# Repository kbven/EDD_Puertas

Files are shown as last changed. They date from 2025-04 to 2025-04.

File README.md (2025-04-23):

# Disseny de les portes

> **Autors:** Brandon Ventura, Pablo Peñalba.

> **Grup Mati**                             

--------

## Objectivo

Diseño de una una PCB para controlar las puertas.

## Especificaciones

* Mecanismo de motor para el alza cristales con un final de carrera.

* Implementación de mecanismo de seguridad anti-atrapamiento para la ventana con sensor de corriente.

* Sistema con motor por apertura y cierre de la puerta.

* Incluir un módulo de lectura RFID para apertura sin llave.
  
  ## Diagrama de Bloques
  
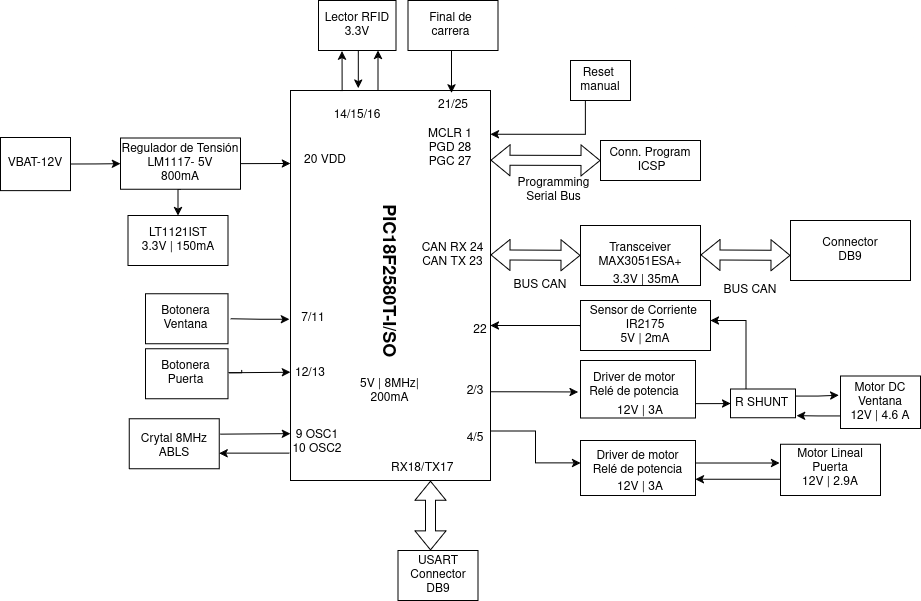
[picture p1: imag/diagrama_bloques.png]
Diagrama_bloques
  
  
  ## Components

| Descripción | Referencia | Package | Datasheet | Proveedor | Precio/unidad | Cantidad |
|:---:|:---:|:---:|:---:|:---:| --- | --- |
| Microcontrolador | PIC18F2580T-I/SO | SOIC-28 | [datasheet](https://ww1.microchip.com/downloads/aemDocuments/documents/OTH/ProductDocuments/DataSheets/39637d.pdf) | [DigiKey](https://www.digikey.es/es/products/detail/microchip-technology/PIC18F2580T-I-SO/739329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) | 7,290 € | 1 |
| Regulador de tensión-5V | LM1117DT-5.0 | TO-252-3  | [datasheet](https://www.ti.com/lit/ds/symlink/lm1117.pdf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) | [Mouser](https://www.mouser.in/ProductDetail/Texas-Instruments/LM1117DT-5.0-NOPB?qs=X1J7HmVL2ZGITaQRKQ6NVA%3D%3D) | 1,610 € | 1 |
| Regulador de tensión 3,3V | LT1121IST-3.3 | SOT-223-3 | [datasheet](https://www.analog.com/media/en/technical-documentation/data-sheets/1121fg.pdf) | [DigiKey](https://www.digikey.at/en/products/detail/analog-devices-inc/LT1121IST-3-3-TRPBF/959066) | 8,190 € | 1 |
| Cristal 8 MHz | AA-8.000MALV-T | SMD | [datasheet](https://www.mouser.es/datasheet/2/417/aa_automotive-14929.pdf) | [Mouser](https://www.mouser.es/ProductDetail/TXC-Corporation/AA-8.000MALV-T?qs=02P6ycQEDWEs8mIQTVoxpQ%3D%3D) | 0,779 € | 1 |
| Pulsadores | 3-1437565-0 | SMD | [datasheet](https://www.mouser.es/datasheet/2/418/7/ENG_CD_2_1437565_7_V-2027970.pdf) | [Mouser](https://www.mouser.es/ProductDetail/TE-Connectivity-PB/3-1437565-0?qs=%2FwXgF%2FfIho%2FDAgSy8ONeew%3D%3D) | 0,266 € | 5 |
| Transceiver | MAX3051ESA+ | SOIC-8 | [datasheet](https://www.mouser.es/datasheet/2/609/MAX3051-3469944.pdf) | [Mouser](https://www.mouser.es/ProductDetail/Analog-Devices-Maxim-Integrated/MAX3051ESA+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) | 3,820 € | 1 |
| Módulo RFID | DLP-RFID2 | THT | [datasheet](https://www.mouser.es/datasheet/2/117/dlp-rfid2-ds-v114-1374531.pdf) | [Mouser](https://www.mouser.es/ProductDetail/DLP-Design/DLP-RFID2?qs=7edrXduW%2FNsZxdz8dNHO%2BQ%3D%3D) | 36,050 € | 1 |
| Conector coaxial | Conector coaxial RS | THT | [datasheet](https://docs.rs-online.com/062e/A700000007510792.pdf) | [RS](https://es.rs-online.com/web/p/conectores-coaxiales/5464049) | 9,630 € | 1 |
| Sensor de Corriente | IR2175STRPBF | SOIC-8 | [datasheet](https://www.mouser.es/datasheet/2/196/Infineon_IR2175_S__DataSheet_v01_00_EN-3362704.pdf) | [Mouser](https://www.mouser.es/ProductDetail/Infineon-Technologies/IR2175STRPBF?qs=2r01AXMCG3Mz96toc2YS0Q%3D%3D) | 3,080 € | 1 |
| Relé de potencia | G6E | THT | [datasheet](https://docs.rs-online.com/8949/A700000008621017.pdf) | [RS](https://es.rs-online.com/web/p/reles-de-potencia/0376593) | 6,180 € | 4 |
| Conector DB9 | 2311765-2 | THT | [datasheet](https://www.mouser.es/datasheet/2/418/7/ENG_CD_2311765_D-2072969.pdf) | [Mouser](https://www.mouser.es/ProductDetail/TE-Connectivity/2311765-2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) | 2,760 € | 2 |
| MOSFET P-Channel | AO3401A | SOT-23-3  | [datasheet](https://www.aosmd.com/sites/default/files/res/datasheets/AO3401A.pdf) | [Digikey](https://www.digikey.es/es/products/detail/alpha-omega-semiconductor-inc/AO3401A/1855773) | 0,420 € | 4 |
| Led verde | LTST-C150KGKT | 1206 | [datasheet](https://www.mouser.es/datasheet/2/239/LTST_C150KGKT-1143771.pdf) | [Mouser](https://www.mouser.es/ProductDetail/LITEON/LTST-C150KGKT?qs=G7lFeYdtIHB%2FzaFKBwEyXw%3D%3D) | 0,171 € | 1 |
| Pin Header 1x3 | 61300311121 | THT | [datasheet](https://www.we-online.com/components/products/datasheet/61300311121.pdf) | [DigiKey](https://www.digikey.es/es/products/detail/w%C3%BCrth-elektronik/61300311121/4846825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) | 0,110 € | 1 |
| Pin Header 1x5 | 61300511121 | THT | [datasheet](https://www.we-online.com/components/products/datasheet/61300511121.pdf) | [DigiKey](https://www.digikey.es/es/products/detail/w-rth-elektronik/61300511121/4846831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) | 0,220 € | 3 |
| Connector screw 1x2 | 1729128 | --- | [datasheet](https://www.phoenixcontact.com/en-us/products/printed-circuit-board-terminal-mkdsn-15-2-508-1729128?type=pdf) | [Mouser](https://www.mouser.es/ProductDetail/Phoenix-Contact/1729128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) | 1,020 € | 3 |
| Connector screw 1x3 | 1751251 | --- | [datasheet](https://www.phoenixcontact.com/en-us/products/printed-circuit-board-terminal-mkds-1-3-35-1751251?type=pdf) | [Mouser](https://www.mouser.es/ProductDetail/Phoenix-Contact/1751251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) | 1,680 € | 2 |
| Resistencias 10K | RK73G2BTTD1002F | 1206 | [datasheet](https://www.koaspeer.com/pdfs/RK73G.pdf) | [Mouser](https://www.mouser.es/ProductDetail/KOA-Speer/RK73G2BTTD1002F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) | 0,241 € | 15 |
| Resistencia 60 | RP73PF1J60R4BTDF | 0603 | [datasheet](https://www.mouser.es/datasheet/2/418/10/ENG_DS_1773272_M1-1588495.pdf) | [Mouser](https://www.mouser.es/ProductDetail/TE-Connectivity-Holsworthy/RP73PF1J60R4BTDF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) | 0,456 € | 1 |
| Resistencia 1K | RNCA0603BTE1K00 | 0603 | [datasheet](https://www.mouser.es/datasheet/2/385/SEI_RNCA-3473065.pdf) | [Mouser](https://www.mouser.es/ProductDetail/SEI-Stackpole/RNCA0603BTE1K00?qs=i8QVZAFTkqR0RAUMHohaTQ%3D%3D) | 0,228 € | 1 |
| Resistencia shunt | WSHM2818R1000FEA | SMD | [datasheet](https://www.vishay.com/docs/30188/wshm2818.pdf) | [Mouser](https://www.mouser.es/ProductDetail/Vishay-Dale/WSHM2818R1000FEA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) | 1,370 € | 1 |
| 10u | ECA-1CHG101I | THT | [datasheet](https://industrial.panasonic.com/cdbs/www-data/pdf/RDF0000/ABA0000C1218.pdf) | [Mouser](https://www.mouser.es/ProductDetail/Panasonic/ECA-1CM100I?qs=fcM5arftASvKR70PPIzFqA%3D%3D) | 0,152 € | 3 |
| 1u | C0805C105K4RACAUTO  | 0805 | [datasheet](https://www.mouser.es/datasheet/2/447/KEM_C1023_X7R_AUTO_SMD-3316698.pdf) | [Mouser](https://www.mouser.es/ProductDetail/KEMET/C0805C105K4RACAUTO?qs=OHu5RF0w3QprP0D5VzlqaQ%3D%3D) | 0,152 € | 1 |
| 100n | C1206C104K4RACTU | 1206 | [datasheet](https://www.mouser.es/datasheet/2/447/KEM_C1002_X7R_SMD-3316098.pdf) | [Mouser](https://www.mouser.es/ProductDetail/KEMET/C1206C104K4RACTU?qs=NAOyRStS94fKvqJx0gg6JQ%3D%3D) | 0,095 € | 7 |
| 21p | 0504N220J500P | 0504 | [datasheet](https://www.knowlescapacitors.com/getattachment/ddd08fe0-16c1-4f86-944e-edc3fc04fb57/X7R.aspx) | [DigiKey](https://www.digikey.es/es/products/detail/knowles-novacap/0504N220J500P/21849946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) | 0,620 € | 2 |
| D6,D7,D8,D9 | SR1202 A0G | THT | [datasheet](https://services.taiwansemi.com/storage/resources/datasheet/SR1202%20SERIES_G2105.pdf) | [Mouser](https://www.mouser.es/ProductDetail/Taiwan-Semiconductor/SR1202-A0G?qs=mAH9sUMRCtsYw%2FEG19A30A%3D%3D) | 0,384 € | 4 |
| D4,D5 | SBR12A45SD1-T | THT | [datasheet](https://www.diodes.com/assets/Datasheets/SBR12A45SD1.pdf) | [Mouser](https://www.mouser.es/ProductDetail/Diodes-Incorporated/SBR12A45SD1-T?qs=oUsD4qhOtFxVeI%252BTfVYIRA%3D%3D) | 0,485 € | 2 |
| D2 | SR1203H | THT | [datasheet](https://services.taiwansemi.com/storage/resources/datasheet/SR1202%20SERIES_G2105.pdf) | [Mouser](https://www.mouser.es/ProductDetail/Taiwan-Semiconductor/SR1203H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) | 0,384 € | 1 |
| D3 | SBR10U45SD1-T | THT | [datasheet](https://www.diodes.com/assets/Datasheets/SBR10U45SD1.pdf) | [Mouser](https://www.mouser.es/ProductDetail/Diodes-Incorporated/SBR10U45SD1-T?qs=oUsD4qhOtFyWKufSWj8qkg%3D%3D) | 0,912 € | 1 |

##Motores y final de carrera

| Descripción | Referencia | Datasheet | Proveedor | Cantidad |
|:---:|:---:|:---:|:---:| --- |
| Motor Lineal | Actuador lineal 12VDC 800N 2,9A | | [Transmotec](https://www.transmotec.es/product/dla-12-30-a-50-ip65/?vat=true) | 1 |
| Motor DC | Motor DC RS PRO | [datasheet](https://docs.rs-online.com/6e47/A700000007082069.pdf) | [Rs](https://es.rs-online.com/web/p/motores-dc/3213186) | 1 |
| Final de carrera | Palanca de Rodillo RS PRO | [datasheet](https://docs.rs-online.com/2b32/A700000008919438.pdf) | [Rs](https://es.rs-online.com/web/p/interruptores-final-de-carrera/9026871) | 2 |

## Historial de cambios

| Data | Autor | Branch | Descripción |
| --- | --- | --- | --- |
| 26/03/2025 | B.Ventura | Main | Readme y Esquemático |
| 26/03/2025 | B.Ventura | Main | Diagrama de Bloques |
| 28/03/2025 | B.Ventura | Main | Terminales y Diodos |
| 28/03/2025 | P.Peñalba | Main | Etiquetas,Botonera y Buck converter |
| 01/04/2025 | B.Ventura | Main | Corrección del esquema, terminal screw terminals y layout v1 |
| 09/04/2025 | B.Ventura | Main | cambio de posición pines, cambio de terminales final de carrera y corrección error grid |
| 09/04/2025 | B.Ventura/P.Peñalba | Main | layout versión 2, reglas de diseño JLCPCB |
| 12/04/2025 | B.Ventura/P.Peñalba | Main | Corrección de las pistas layout y planos |
| 21/04/2025 | B.Ventura | Main | Presupuesto |

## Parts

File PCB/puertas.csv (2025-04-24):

# | Reference | Footprint | Qty | Value
1 | C1,C2,C7,C8,C9,C10,C13 | Capacitor_SMD:C_1206_3216Metric | 7 | 100n
2 | C3,C4 | Capacitor_THT:CP_Radial_D5.0mm_P2.50mm | 2 | 10u
3 | C5,C6 | Capacitor_SMD:C_0504_1310Metric | 2 | 21p
4 | C11 | Capacitor_THT:CP_Radial_D6.3mm_P2.50mm | 1 | 10u
5 | C12 | Capacitor_SMD:C_0805_2012Metric | 1 | 1uF
6 | D1 | LED_SMD:LED_1206_3216Metric | 1 | LED
7 | D2,D4,D5,D6,D7,D8,D9 | Diode_THT:D_DO-201AD_P12.70mm_Horizontal | 7 | D
8 | D3 | Diode_THT:D_DO-15_P12.70mm_Horizontal | 1 | D_Zener
9 | IC1 | MAX3051ESA+:SOIC127P600X175-8N | 1 | MAX3051ESA+
10 | IC2 | IR2175STRPBF:SOIC127P600X175-8N | 1 | IR2175STRPBF
11 | J1 | Connector_Dsub:DSUB-9_Pins_Horizontal_P2.77x2.84mm_EdgePinOffset4.94mm_Housed_MountingHolesOffset4.94mm | 1 | DE9_USART
12 | J2 | Connector_PinHeader_2.54mm:PinHeader_1x05_P2.54mm_Vertical | 1 | ICSP
13 | J3 | Connector_Dsub:DSUB-9_Pins_Horizontal_P2.77x2.84mm_EdgePinOffset4.94mm_Housed_MountingHolesOffset4.94mm | 1 | DE9_CAN
14 | J4 | Connector_Coaxial:BNC_TEConnectivity_1478035_Horizontal | 1 | Conn_Coaxial
15 | J5 | TerminalBlock_Phoenix:TerminalBlock_Phoenix_MKDS-3-2-5.08_1x02_P5.08mm_Horizontal | 1 | BAT_CONN
16 | J6 | Connector_PinHeader_2.54mm:PinHeader_1x03_P2.54mm_Vertical | 1 | PROG
17 | J7 | Connector_PinHeader_2.54mm:PinHeader_1x05_P2.54mm_Vertical | 1 | DOOR
18 | J8 | Connector_PinHeader_2.54mm:PinHeader_1x05_P2.54mm_Vertical | 1 | WINDOW
19 | J9 | TerminalBlock_Phoenix:TerminalBlock_Phoenix_MKDS-3-2-5.08_1x02_P5.08mm_Horizontal | 1 | motor_lineal
20 | J10 | TerminalBlock_Phoenix:TerminalBlock_Phoenix_MKDS-3-3-5.08_1x03_P5.08mm_Horizontal | 1 | FINAL_ALTO
21 | J12 | TerminalBlock_Phoenix:TerminalBlock_Phoenix_MKDS-3-2-5.08_1x02_P5.08mm_Horizontal | 1 | motor_dc
22 | J13 | TerminalBlock_Phoenix:TerminalBlock_Phoenix_MKDS-3-3-5.08_1x03_P5.08mm_Horizontal | 1 | FINAL_BAJO
23 | K1,K2,K3,K4 | Relay_THT:Relay_SPDT_Omron_G6E | 4 | G6E
24 | pull-down1,pull-down2,pull-down3,pull-down4,R11,R12,R13,R16,R17 | Capacitor_SMD:C_1206_3216Metric | 9 | 10k
25 | Q1,Q2,Q3,Q4 | Package_TO_SOT_SMD:SOT-23 | 4 | AO3401A
26 | R1 | Resistor_SMD:R_1206_3216Metric_Pad1.30x1.75mm_HandSolder | 1 | 10K
27 | R2 | Resistor_SMD:R_0603_1608Metric | 1 | 60
28 | R3,R4,R5,R6,R8 | Resistor_SMD:R_1206_3216Metric | 5 | 10k
29 | R7 | Resistor_SMD:R_0603_1608Metric | 1 | 1k
30 | R9 | Resistor_SMD:R_Shunt_Ohmite_LVK25 | 1 | R_Shunt
31 | R10 | Capacitor_SMD:C_1206_3216Metric | 1 | 0
32 | S1,S2,S3,S6,S7 | 3-1437565-0:314375650 | 5 | 3-1437565-0
33 | U1 | DLP-RFID2:DLP-RFID2 | 1 | DLP-RFID2
34 | U3 | LT1121IST-3.3-TRPBF:SOT-223_ST_LIT | 1 | LT1121IST-3.3-TRPBF
35 | U4 | PIC18F2580T_I_SO:SOIC28-W_MC_MCH | 1 | PIC18F2580T-I/SO
36 | U5 | Package_TO_SOT_SMD:TO-252-3_TabPin2 | 1 | LM1117DT-5.0
37 | Y2 | AA-8.000MALV-T:AA8000MALVT | 1 | AA-8.000MALV-T

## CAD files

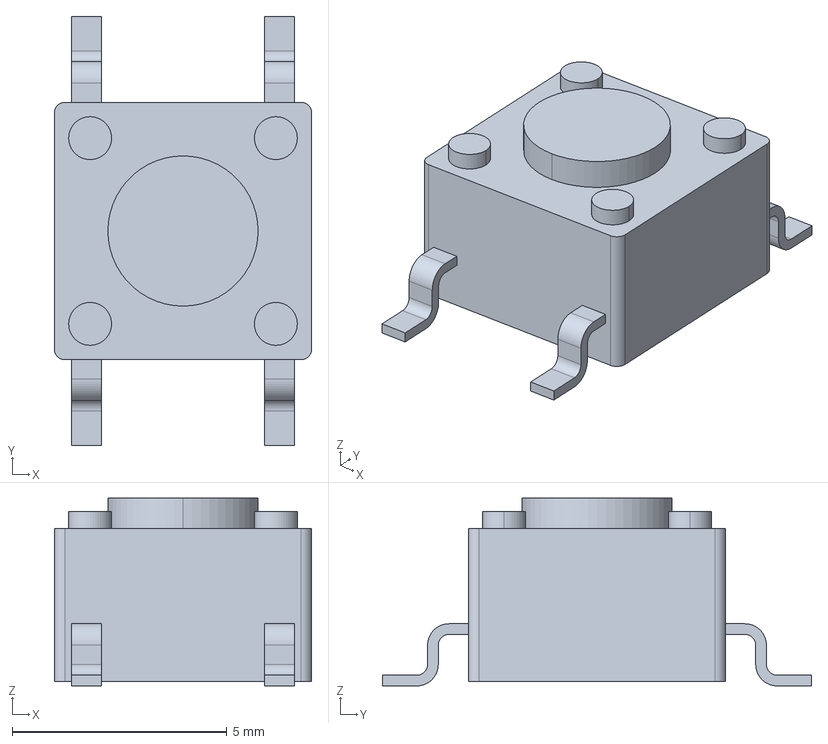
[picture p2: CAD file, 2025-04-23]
PCB/componentes/3-1437565-0/3D/3-1437565-0.stp
6.00 x 10.0 x 4.38 mm

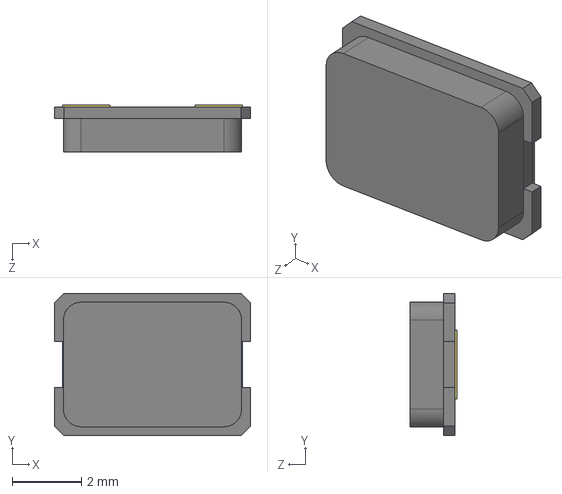
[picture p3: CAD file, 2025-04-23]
PCB/componentes/AA-8.000MALV-T/3D/AA-8.000MALV-T.stp
5.67 x 4.12 x 1.35 mm

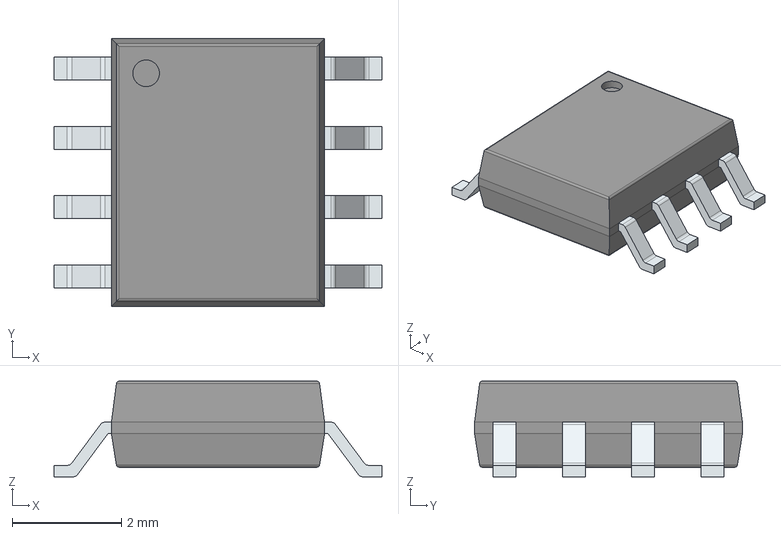
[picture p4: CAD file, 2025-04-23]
PCB/componentes/IR2175STRPBF/3D/IR2175STRPBF.stp
6.00 x 4.90 x 1.75 mm
PinsArrayLR

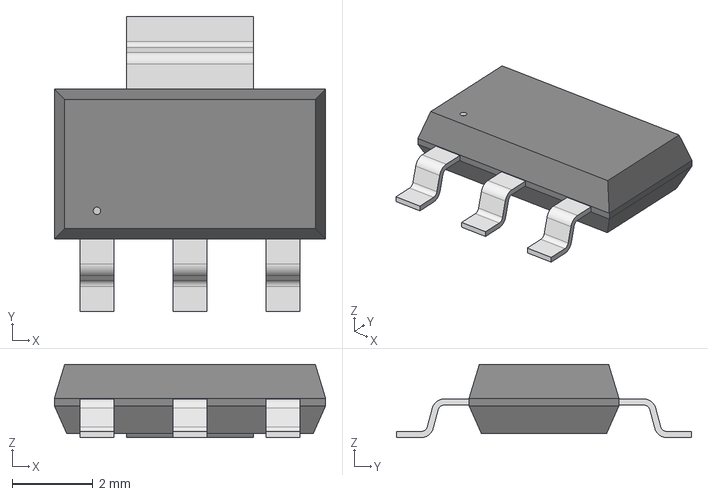
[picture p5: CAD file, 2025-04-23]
PCB/componentes/LT1121IST/3d/SOT-223_ST_LIT.step
6.71 x 7.29 x 1.81 mm

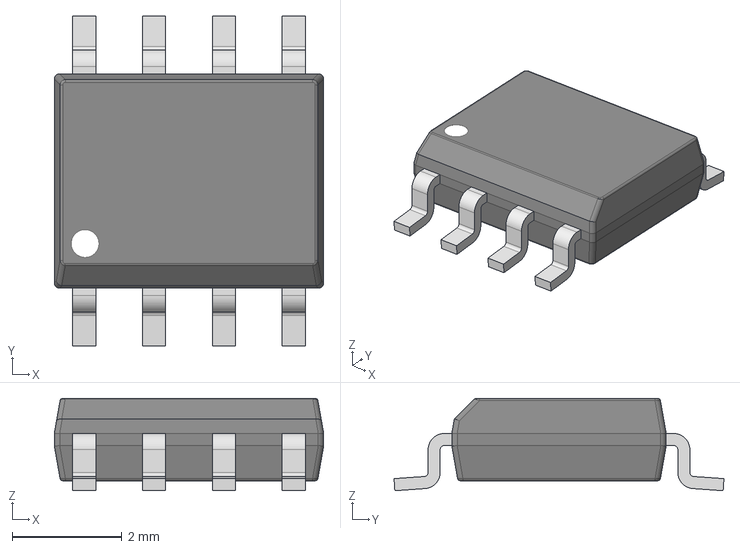
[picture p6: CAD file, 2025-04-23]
PCB/componentes/MAX3051ESA+/3D/MAX3051ESA+T.stp
4.90 x 6.00 x 1.68 mm

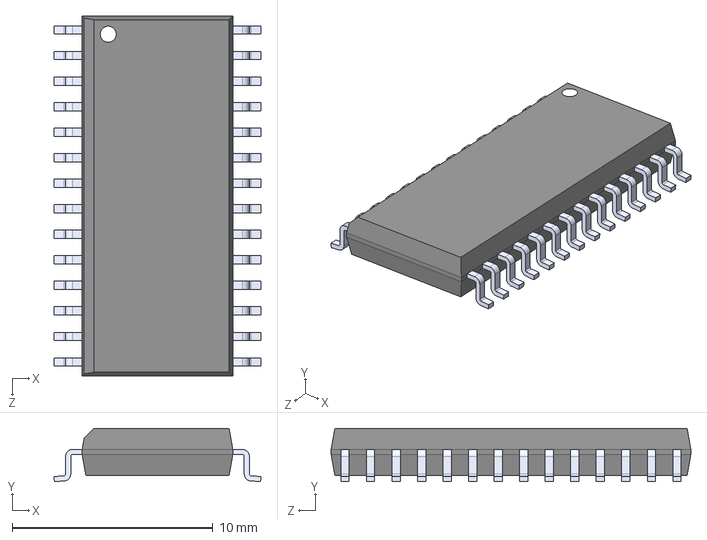
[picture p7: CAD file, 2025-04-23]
PCB/componentes/PIC18F2580T_I_SO/3d model/PIC18F2580T-I_SO.STEP
10.3 x 2.65 x 17.9 mm

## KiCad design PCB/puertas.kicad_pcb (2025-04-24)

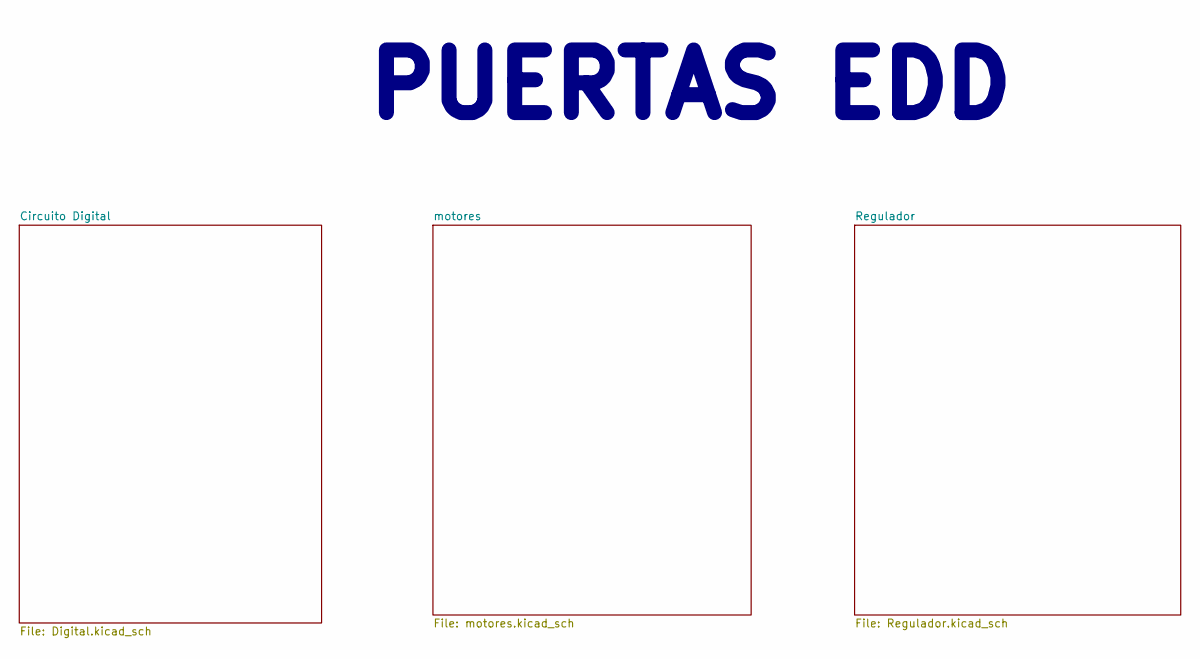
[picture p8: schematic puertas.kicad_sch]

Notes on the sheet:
PUERTAS EDD

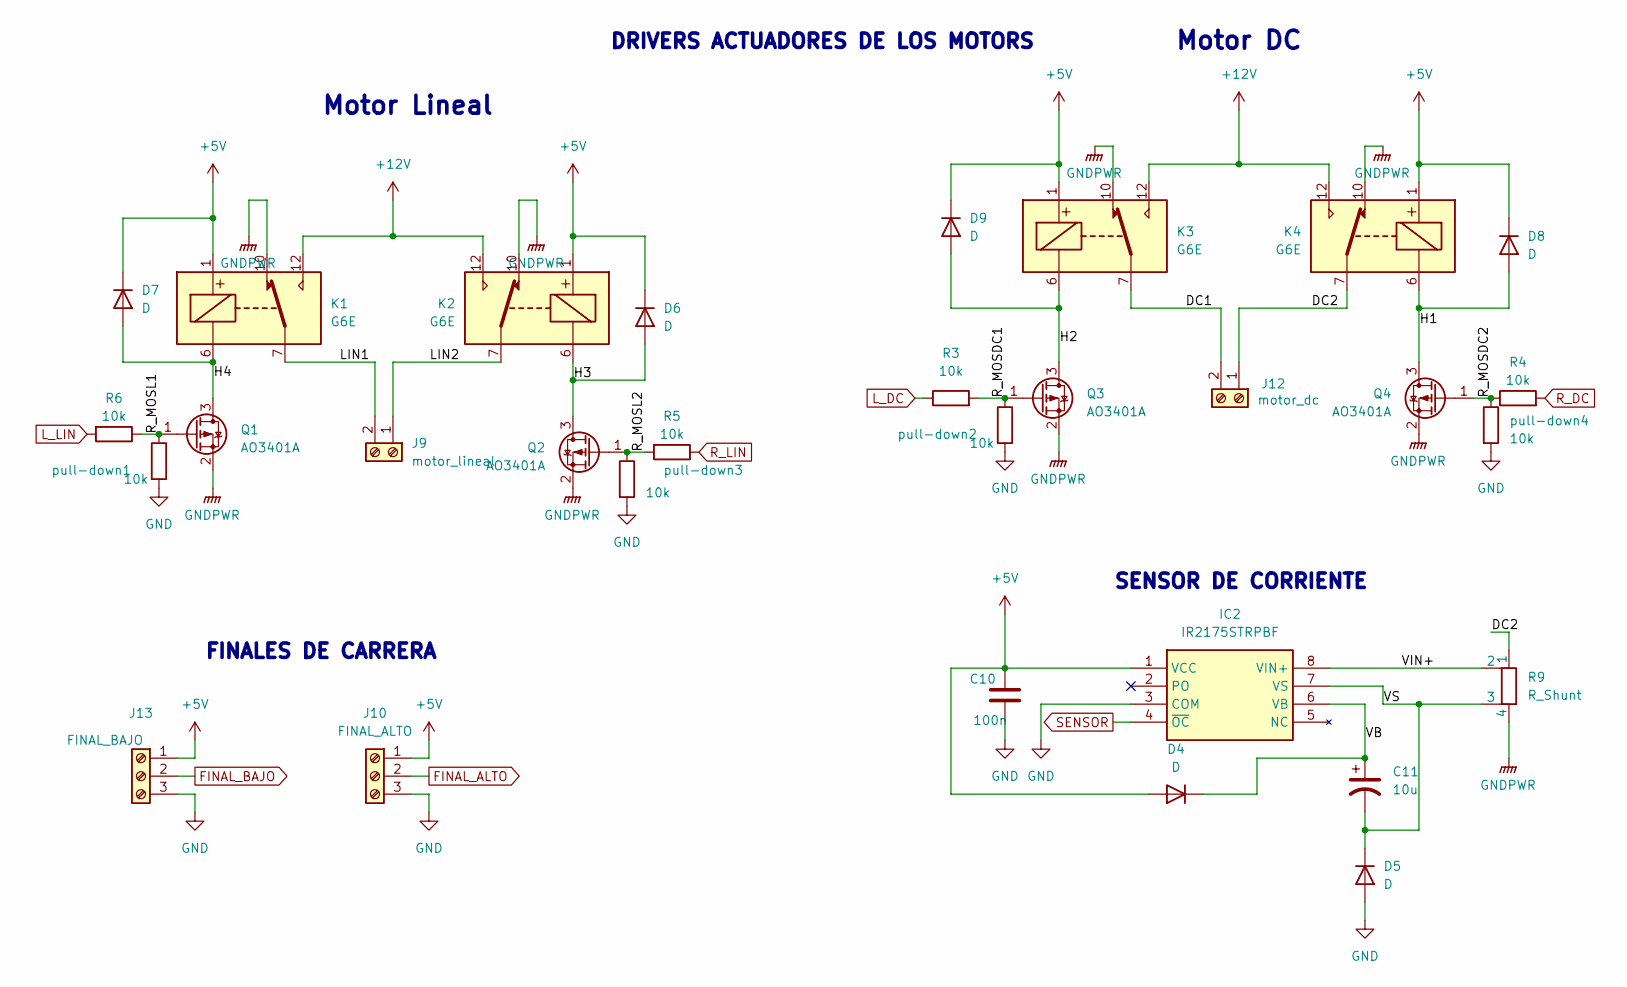
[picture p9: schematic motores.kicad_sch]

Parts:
C10: 100n; C_1206_3216Metric
C11: 10u; CP_Radial_D6.3mm_P2.50mm
D4, D5, D6, D7, D8, D9: D; D_DO-201AD_P12.70mm_Horizontal
IC2: IR2175STRPBF; SOIC127P600X175-8N; Mouser Part Number 942-IR2175STRPBF
J9: motor_lineal; TerminalBlock_Phoenix_MKDS-3-2-5.08_1x02_P5.08mm_Horizontal
J10: FINAL_ALTO; TerminalBlock_Phoenix_MKDS-3-3-5.08_1x03_P5.08mm_Horizontal
J12: motor_dc; TerminalBlock_Phoenix_MKDS-3-2-5.08_1x02_P5.08mm_Horizontal
J13: FINAL_BAJO; TerminalBlock_Phoenix_MKDS-3-3-5.08_1x03_P5.08mm_Horizontal
K1, K2, K3, K4: G6E; Relay_SPDT_Omron_G6E
Q1, Q2, Q3, Q4: AO3401A; SOT-23
R3, R4, R5, R6: 10k; R_1206_3216Metric
R9: R_Shunt; R_Shunt_Ohmite_LVK25
pull-down1, pull-down2, pull-down3, pull-down4: 10k; C_1206_3216Metric

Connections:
+5V: C10.1, D4.2 (A), D6.1 (K), D7.1 (K), D8.1 (K), D9.1 (K), IC2.1 (VCC), J10.1, J13.1, K1.1, K2.1, K3.1, K4.1; also elsewhere on the board
+12V: K1.12, K2.12, K3.12, K4.12; also elsewhere on the board
/motores/DC1: J12.2, K3.7
/motores/DC2: J12.1, K4.7, R9.1
/motores/H1: D8.2 (A), K4.6, Q4.3 (D)
/motores/H2: D9.2 (A), K3.6, Q3.3 (D)
/motores/H3: D6.2 (A), K2.6, Q2.3 (D)
/motores/H4: D7.2 (A), K1.6, Q1.3 (D)
/motores/LIN1: J9.2, K1.7
/motores/LIN2: J9.1, K2.7
/motores/R_MOSDC1: Q3.1 (G), R3.2, pull-down2.1
/motores/R_MOSDC2: Q4.1 (G), R4.1, pull-down4.1
/motores/R_MOSL1: Q1.1 (G), R6.1, pull-down1.1
/motores/R_MOSL2: Q2.1 (G), R5.2, pull-down3.1
/motores/VB: C11.1, D4.1 (K), IC2.6 (VB)
/motores/VIN+: IC2.8 (VIN+), R9.2
/motores/VS: C11.2, D5.1 (K), IC2.7 (VS), R9.3
FINAL_ALTO: J10.2; also elsewhere on the board
FINAL_BAJO: J13.2; also elsewhere on the board
GND: C10.2, D5.2 (A), IC2.3 (COM), J10.3, J13.3, pull-down1.2, pull-down2.2, pull-down3.2, pull-down4.2; also elsewhere on the board
GNDPWR: K1.10, K2.10, K3.10, K4.10, Q1.2 (S), Q2.2 (S), Q3.2 (S), Q4.2 (S), R9.4; also elsewhere on the board
L_DC: R3.1; also elsewhere on the board
L_LIN: R6.2; also elsewhere on the board
R_DC: R4.2; also elsewhere on the board
R_LIN: R5.1; also elsewhere on the board
SENSOR: IC2.4 (~OC); also elsewhere on the board

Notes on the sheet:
FINALES DE CARRERA
Motor DC
Motor Lineal
DRIVERS ACTUADORES DE LOS MOTORS
SENSOR DE CORRIENTE

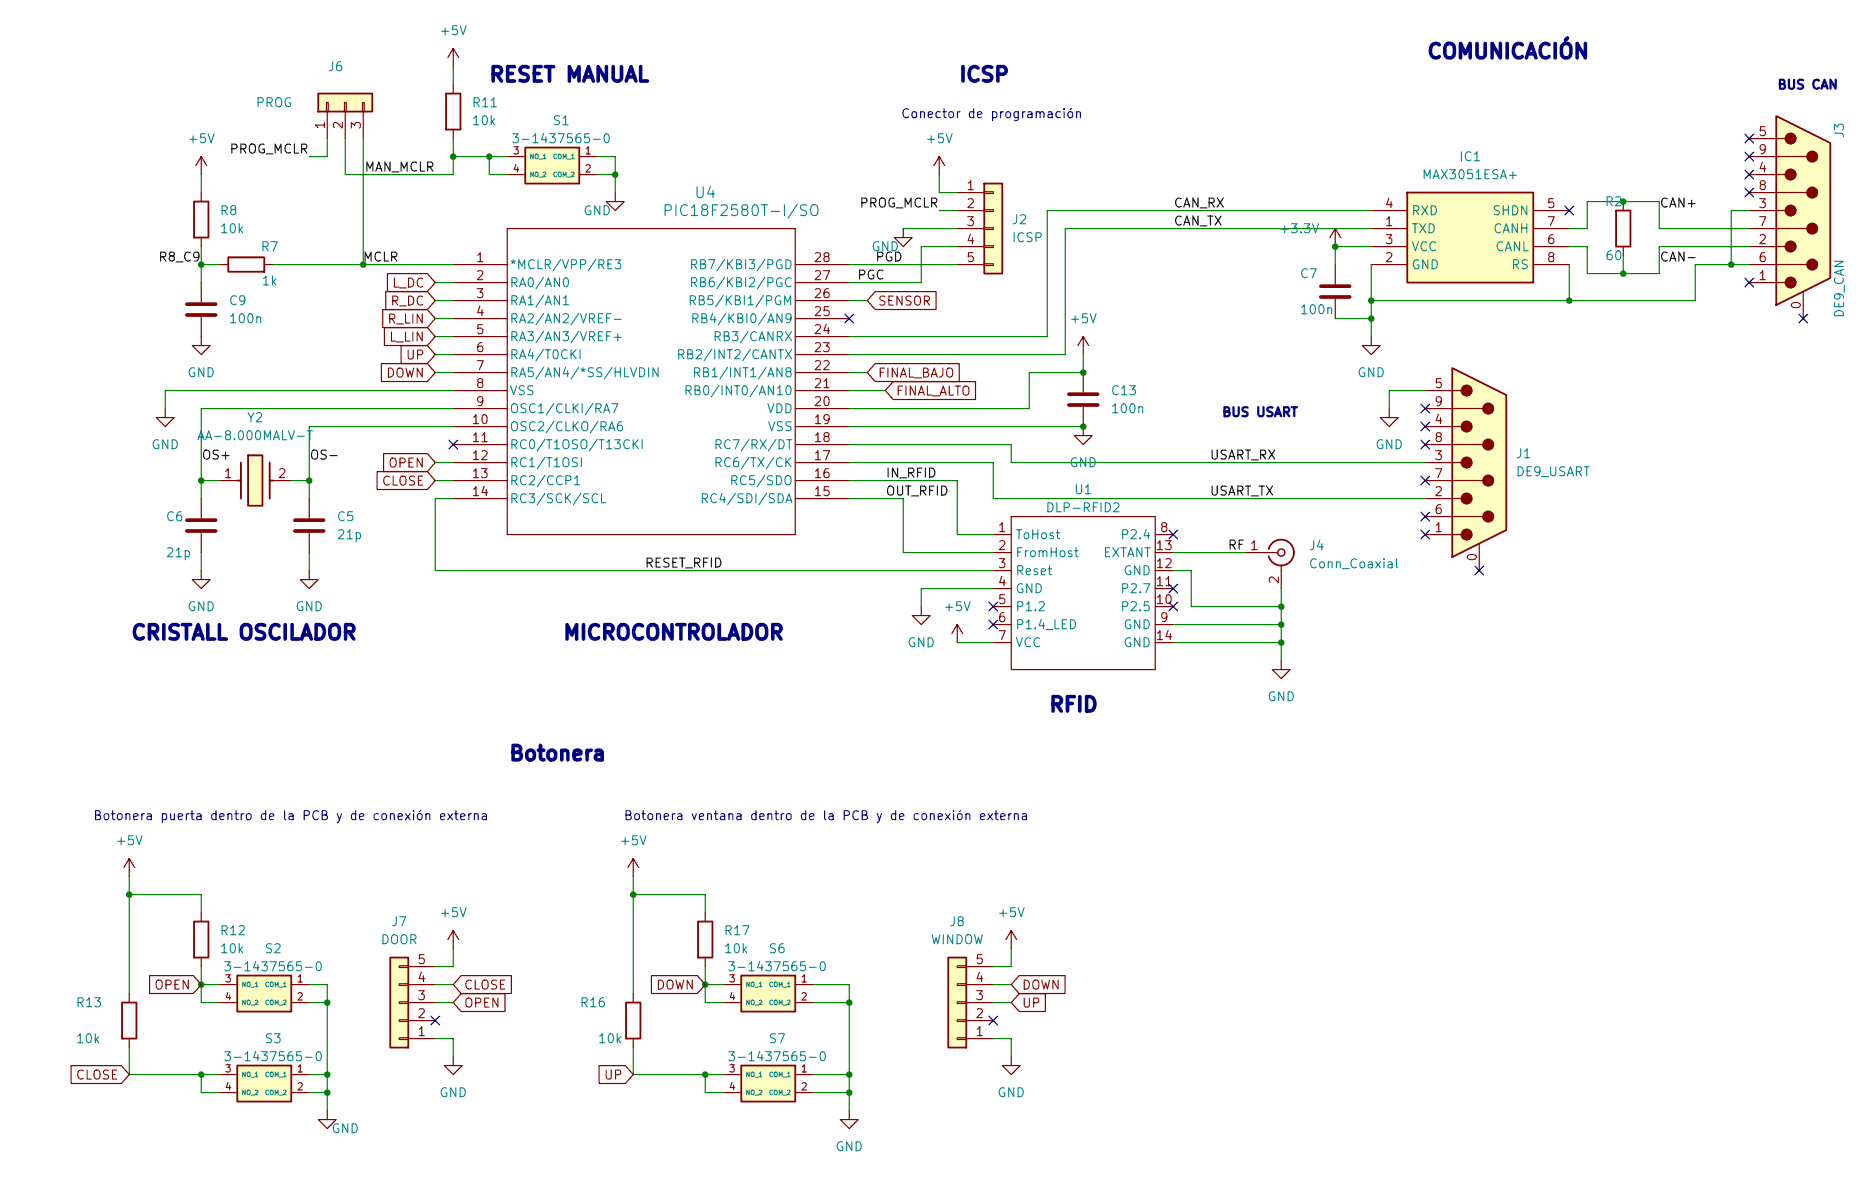
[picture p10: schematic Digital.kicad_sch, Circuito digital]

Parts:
C5, C6: 21p; C_0504_1310Metric
C7, C9, C13: 100n; C_1206_3216Metric
IC1: MAX3051ESA+; SOIC127P600X175-8N; Mouser Part Number 700-MAX3051ESA
J1: DE9_USART; DSUB-9_Pins_Horizontal_P2.77x2.84mm_EdgePinOffset4.94mm_Hou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
J2: ICSP; PinHeader_1x05_P2.54mm_Vertical
J3: DE9_CAN; DSUB-9_Pins_Horizontal_P2.77x2.84mm_EdgePinOffset4.94mm_Hou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; LCSC C575183
J4: Conn_Coaxial; BNC_TEConnectivity_1478035_Horizontal
J6: PROG; PinHeader_1x03_P2.54mm_Vertical
J7: DOOR; PinHeader_1x05_P2.54mm_Vertical
J8: WINDOW; PinHeader_1x05_P2.54mm_Vertical
R2: 60; R_0603_1608Metric; LCSC C22787
R7: 1k; R_0603_1608Metric
R8: 10k; R_1206_3216Metric
R11, R12, R13, R16, R17: 10k; C_1206_3216Metric
S1, S2, S3, S6, S7: 3-1437565-0; 314375650; Mouser Part Number 506-3-1437565-0
U1: DLP-RFID2
U4: PIC18F2580T-I/SO; SOIC28-W_MC_MCH
Y2: AA-8.000MALV-T; AA8000MALVT; Mouser Part Number 717-AA-8.000MALV-T

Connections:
+3.3V: C7.1, IC1.3 (VCC); also elsewhere on the board
+5V: C13.1, J2.1, J7.5, J8.5, R8.1, R11.1, R12.1, R13.1, R16.1, R17.1, U1.7 (VCC), U4.20 (VDD); also elsewhere on the board
/Circuito Digital/CAN+: IC1.7 (CANH), J3.7, R2.2
/Circuito Digital/CAN-: IC1.6 (CANL), J3.2, R2.1
/Circuito Digital/CAN_RX: IC1.4 (RXD), U4.24 (RB3/CANRX)
/Circuito Digital/CAN_TX: IC1.1 (TXD), U4.23 (RB2/INT2/CANTX)
/Circuito Digital/IN_RFID: U1.1 (ToHost), U4.16 (RC5/SDO)
/Circuito Digital/MAN_MCLR: J6.2, R11.2, S1.3 (NO_1), S1.4 (NO_2)
/Circuito Digital/MCLR: J6.3, R7.2, U4.1 (*MCLR/VPP/RE3)
/Circuito Digital/OS+: C6.1, U4.9 (OSC1/CLKI/RA7), Y2.1
/Circuito Digital/OS-: C5.1, U4.10 (OSC2/CLKO/RA6), Y2.2
/Circuito Digital/OUT_RFID: U1.2 (FromHost), U4.15 (RC4/SDI/SDA)
/Circuito Digital/PGC: J2.4, U4.27 (RB6/KBI2/PGC)
/Circuito Digital/PGD: J2.5, U4.28 (RB7/KBI3/PGD)
/Circuito Digital/PROG_MCLR: J2.2, J6.1
/Circuito Digital/R8_C9: C9.1, R7.1, R8.2
/Circuito Digital/RESET_RFID: U1.3 (Reset), U4.14 (RC3/SCK/SCL)
/Circuito Digital/RF: J4.1 (In), U1.13 (EXTANT)
/Circuito Digital/USART_RX: J1.3, U4.18 (RC7/RX/DT)
/Circuito Digital/USART_TX: J1.2, U4.17 (RC6/TX/CK)
CLOSE: J7.4, R13.2, S3.3 (NO_1), S3.4 (NO_2), U4.13 (RC2/CCP1)
DOWN: J8.4, R17.2, S6.3 (NO_1), S6.4 (NO_2), U4.7 (RA5/AN4/*SS/HLVDIN)
FINAL_ALTO: U4.21 (RB0/INT0/AN10); also elsewhere on the board
FINAL_BAJO: U4.22 (RB1/INT1/AN8); also elsewhere on the board
GND: C5.2, C6.2, C7.2, C9.2, C13.2, IC1.2 (GND), IC1.8 (RS), J1.5, J2.3, J3.3, J3.6, J4.2 (Ext), J7.1, J8.1, S1.1 (COM_1), S1.2 (COM_2), S2.1 (COM_1), S2.2 (COM_2), S3.1 (COM_1), S3.2 (COM_2), S6.1 (COM_1), S6.2 (COM_2), S7.1 (COM_1), S7.2 (COM_2), U1.4 (GND), U1.9 (GND), U1.12 (GND), U1.14 (GND), U4.8 (VSS), U4.19 (VSS); also elsewhere on the board
L_DC: U4.2 (RA0/AN0); also elsewhere on the board
L_LIN: U4.5 (RA3/AN3/VREF+); also elsewhere on the board
OPEN: J7.3, R12.2, S2.3 (NO_1), S2.4 (NO_2), U4.12 (RC1/T1OSI)
R_DC: U4.3 (RA1/AN1); also elsewhere on the board
R_LIN: U4.4 (RA2/AN2/VREF-); also elsewhere on the board
SENSOR: U4.26 (RB5/KBI1/PGM); also elsewhere on the board
UP: J8.3, R16.2, S7.3 (NO_1), S7.4 (NO_2), U4.6 (RA4/T0CKI)

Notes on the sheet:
CRISTALL OSCILADOR
BUS USART
RESET MANUAL
Botonera
RFID
COMUNICACIÓN
MICROCONTROLADOR
Botonera puerta dentro de la PCB y de conexión externa
ICSP
Conector de programación
BUS CAN
Botonera ventana dentro de la PCB y de conexión externa

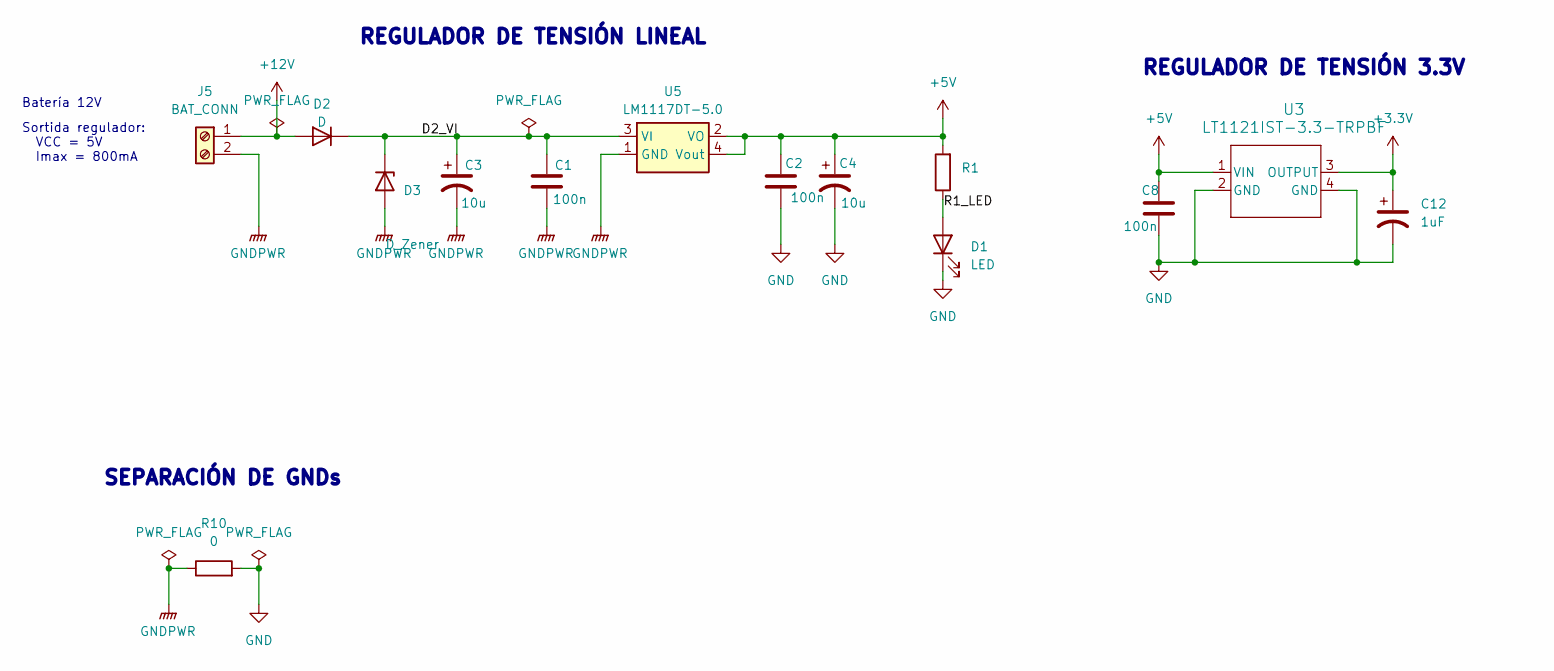
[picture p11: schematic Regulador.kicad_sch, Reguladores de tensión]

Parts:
C1, C2, C8: 100n; C_1206_3216Metric
C3, C4: 10u; CP_Radial_D5.0mm_P2.50mm
C12: 1uF; C_0805_2012Metric
D1: LED; LED_1206_3216Metric
D2: D; D_DO-201AD_P12.70mm_Horizontal
D3: D_Zener; D_DO-15_P12.70mm_Horizontal
J5: BAT_CONN; TerminalBlock_Phoenix_MKDS-3-2-5.08_1x02_P5.08mm_Horizontal
R1: 10K; R_1206_3216Metric_Pad1.30x1.75mm_HandSolder
R10: 0; C_1206_3216Metric
U3: LT1121IST-3.3-TRPBF; SOT-223_ST_LIT
U5: LM1117DT-5.0; TO-252-3_TabPin2

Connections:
+3.3V: C12.1, U3.3 (OUTPUT); also elsewhere on the board
+5V: C2.1, C4.1, C8.1, R1.2, U3.1 (VIN), U5.2 (VO), U5.4 (Vout); also elsewhere on the board
+12V: D2.2 (A), J5.1; also elsewhere on the board
/Regulador/D2_VI: C1.1, C3.1, D2.1 (K), D3.1 (K), U5.3 (VI)
/Regulador/R1_LED: D1.2 (A), R1.1
GND: C2.2, C4.2, C8.2, C12.2, D1.1 (K), R10.2, U3.2 (GND), U3.4 (GND); also elsewhere on the board
GNDPWR: C1.2, C3.2, D3.2 (A), J5.2, R10.1, U5.1 (GND); also elsewhere on the board

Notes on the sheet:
SEPARACIÓN DE GNDs
Sortida regulador: VCC = 5V Imax = 800mA
REGULADOR DE TENSIÓN 3.3V
REGULADOR DE TENSIÓN LINEAL
Batería 12V

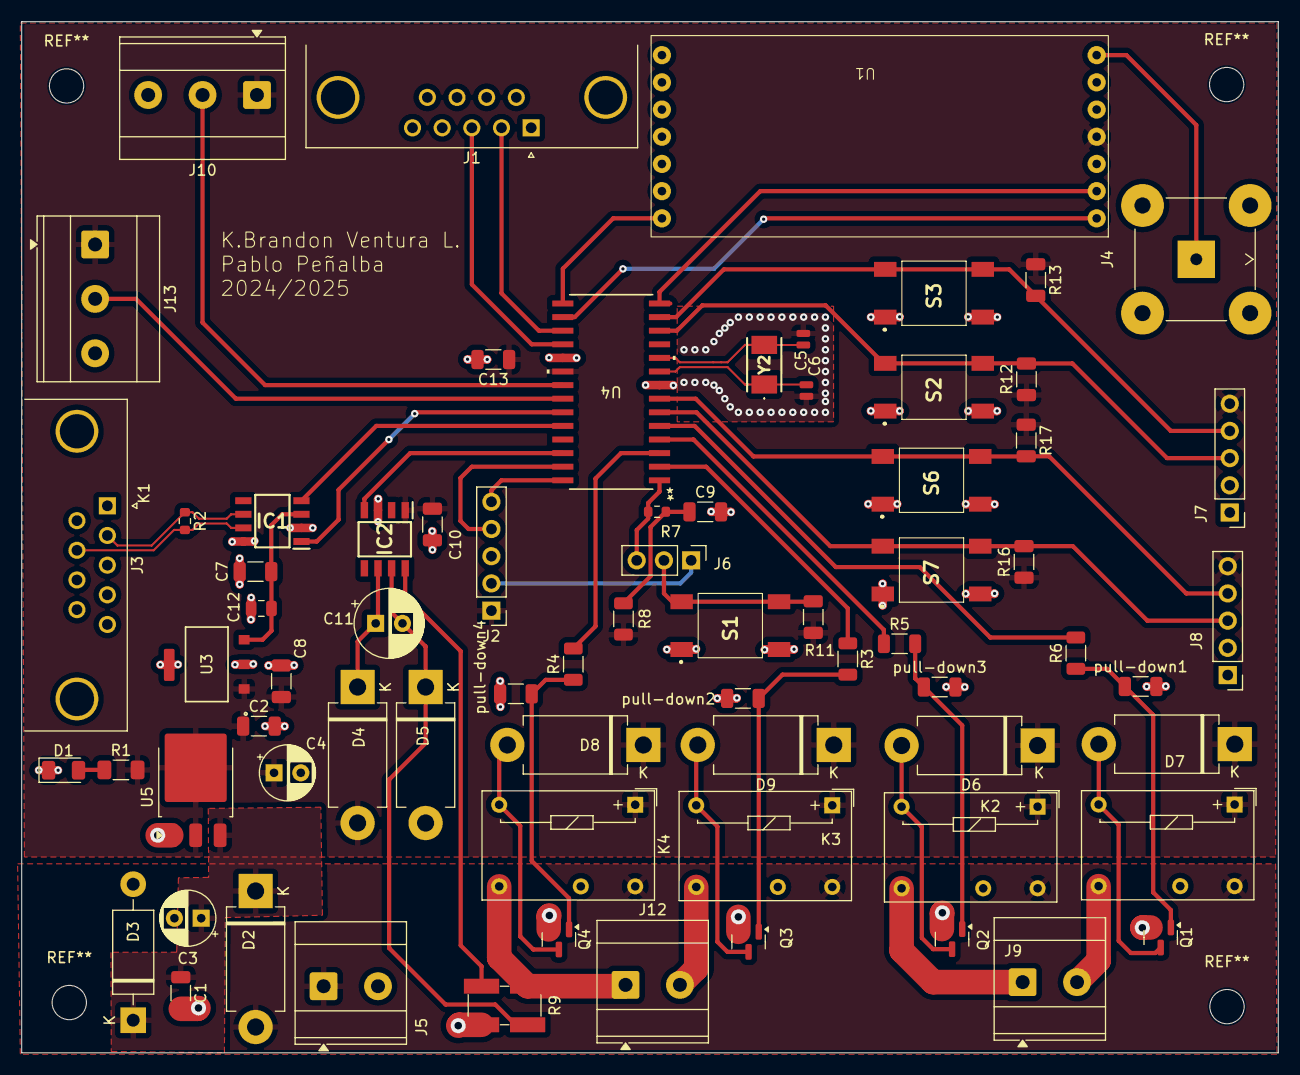
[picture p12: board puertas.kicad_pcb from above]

Board: 2 copper layers, 117.3 x 96.3 mm, 73 parts (1 on the bottom side), 51 nets.

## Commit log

2025-03-26 Circuit failed cadlab corregido
2025-03-26 diagrama de bloques
2025-03-28 Terminales y Diodos
    Terminales de motor tipo screw y diodos de relés
    [motores.kicad_sch]
2025-03-28 Test commit
    valores de condensadores de cristal
    [Digital.kicad_sch]
2025-03-29 added datasheets for buck, ldo and button
2025-03-29 modificado el LM1117 a la versión TO-252 de 3 patas y salida no ajustable a 5V. Añadido el coil de salida 82683C para el BUCK a la librería
    [Regulador.kicad_sch]
2025-03-29 conectados directamente los relés a los conectores
    [motores.kicad_sch]
2025-03-29 anadido el shdn directo al PIC. Es un pin de alarma térmica del transceiver. El sensor de corriente está mal hay que darle una vuelta
    [Digital.kicad_sch, Regulador.kicad_sch, motores.kicad_sch]
2025-03-30 Condesnadors buck converter
    [Regulador.kicad_sch]
2025-04-02 layout pre
    [puertas.kicad_pcb]
2025-04-02 esquemático v2
    [Digital.kicad_sch, Regulador.kicad_sch, motores.kicad_sch]
2025-04-05 Fixed motors
    mosfet shcematic fix
    [motores.kicad_sch]
2025-04-05 smaller diodes for rele
2025-04-05 changed relay
2025-04-09 Fixed labels and ERC errors
    [Digital.kicad_sch, Regulador.kicad_sch, motores.kicad_sch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]
2025-04-09 ADDED footprint RFID lector
    [Digital.kicad_sch, puertas.kicad_pcb]
2025-04-09 cambio de posición de los pines
    [Digital.kicad_sch]
2025-04-09 cambio de terminales tipo screw, final de carrera
    [motores.kicad_sch]
2025-04-09 corrección de error de grid
    [Regulador.kicad_sch]
2025-04-09 layout v2, reglas jlcpcb
    [puertas.kicad_pcb]
2025-04-09 added links for diodes to mouser.md
2025-04-09 ancho de pista de gnd, corrección de ruteado
    corrección de separación de plano de +5V, ancho de pista coincidente con gnd
    [puertas.kicad_pcb]
2025-04-23 Componentes PCB
    [3-1437565-0.stp, AA-8.000MALV-T.stp, IR2175STRPBF.stp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]
2025-04-24 Update PCB
    [Digital.kicad_sch, Regulador.kicad_sch, motores.kicad_sch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]
2025-04-24 Delete PCB/sym-lib-table
    no utilizado
2025-04-24 archivo BOM
    [puertas.csv]
2025-04-24 Coste de fabricación
    [Presupuesto_fabriacion.xls]
